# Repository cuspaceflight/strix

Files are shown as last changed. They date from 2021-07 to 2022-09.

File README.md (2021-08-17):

<p align="center">
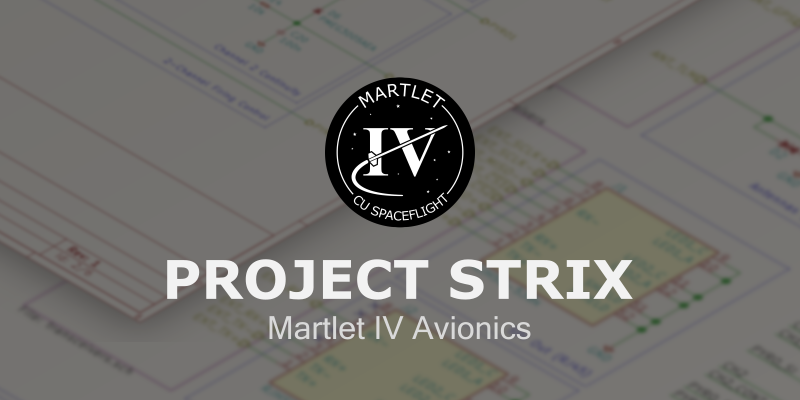
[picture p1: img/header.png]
	
</p>

This repository contains the schematics and firmware for the Martlet IV
Avionics system - Project Strix.

Project Strix is a single-board flight computer designed to carry out essential
tasks during the launch of Martlet IV. Powered by an ARM Cortex-M4, Strix is
able to perform a plethora of functions in real time, and respond to dynamic
events as they happen.

## Specification
The system must be able to
1. Carry out data acquisition for the Pulsar engine sensors.
2. Perform altimetry for the rocket for the purpose of:
	1. Finding the maximum altitude obtained by the rocket.
	2. Deploying the parachutes<sup>*</sup>.
3. Store the data obtained from 1. and 2. using a storage device in a
	protective container.
4. Transmit the data obtained from 1. and 2. to a ground station in
	real-time for the purpose of:
	1. Informing the ground support team of the Pulsar engine sensor
		data before launch (i.e. during filling operations).
	2. To aid an investigation should the rocket vehicle suffer an
		in-flight malfunction.
	3. To find out the rocket's maximum altitude in case loss of
		the rocket prevents retrieval of stored data.

<sup>*</sup>Note that a commercial off-the-shelf 'Stratologger' altimeter
	will also be wired to the parachutes and will also be able to
	deploy them for redundancy.

## Core Modules
The system is composed of several sub-modules, all connected to the central
microcontroller for unified control.

### Altimeter
The onboard altimeter uses two redundant IMUs and barometric pressure sensors
to accurately determine the altitude of the rocket.

### Sensor Front-Ends
The sensor front-ends take data from the Pulsar engine sensors and converts them
into voltages readable by the microcontroller's onboard ADCs. The subsystem
supports the following sensors:

Sensor             | Quantity | Model
------------------ | -------- | --------------------------------------------------------
Pressure Tranducer | 2        | [Omega PXM319-070GI][p_sensor]
Thermocouple       | 4        | [RS Pro K-type welded tip 1/0.315m 5m (762-1118)][t_sensor]

### Radio
The radio subsystem handles the onboard two-way ISM-band radio, which allows
Strix to both send telemetry to ground control and receive telecommands. A
modular architecture allows for precice control of output power to ensure
the rocket operates within local limits. The subsystem also contains a GPS
receiver, which assists in location of the rocket after landing.

### PSU
The modular power supply provides regulated 1.8V, 3.3V, and 12V power to the
flight computer and blackbox. Power is delivered from 2x 18650 Li-ion cells,
which can be recharged on the pad before switching to internal power.

## Design Constraints
The space allowed for the system is shown below (dimensions
in mm):

<p align="center">
	
</p>

The module must also not take up the entire space; some area or a hole
must be left empty to allow other cables to pass through the rocket
(in addition to the central hole).

The module, including any batteries and mounting hardware, should have
as little mass as possible - it must weigh no more than 500g.

[spec]: https://docs.google.com/document/d/1wuNd2ukuNRVKfNca_YTkUf5Qp6ZxcXcQoBAJ7XX6a5Y
[p_sensor]: https://br.omega.com/omegaFiles/pressure/pdf/PXM309.pdf
[t_sensor]: https://docs.rs-online.com/4918/0900766b815bb169.pdf

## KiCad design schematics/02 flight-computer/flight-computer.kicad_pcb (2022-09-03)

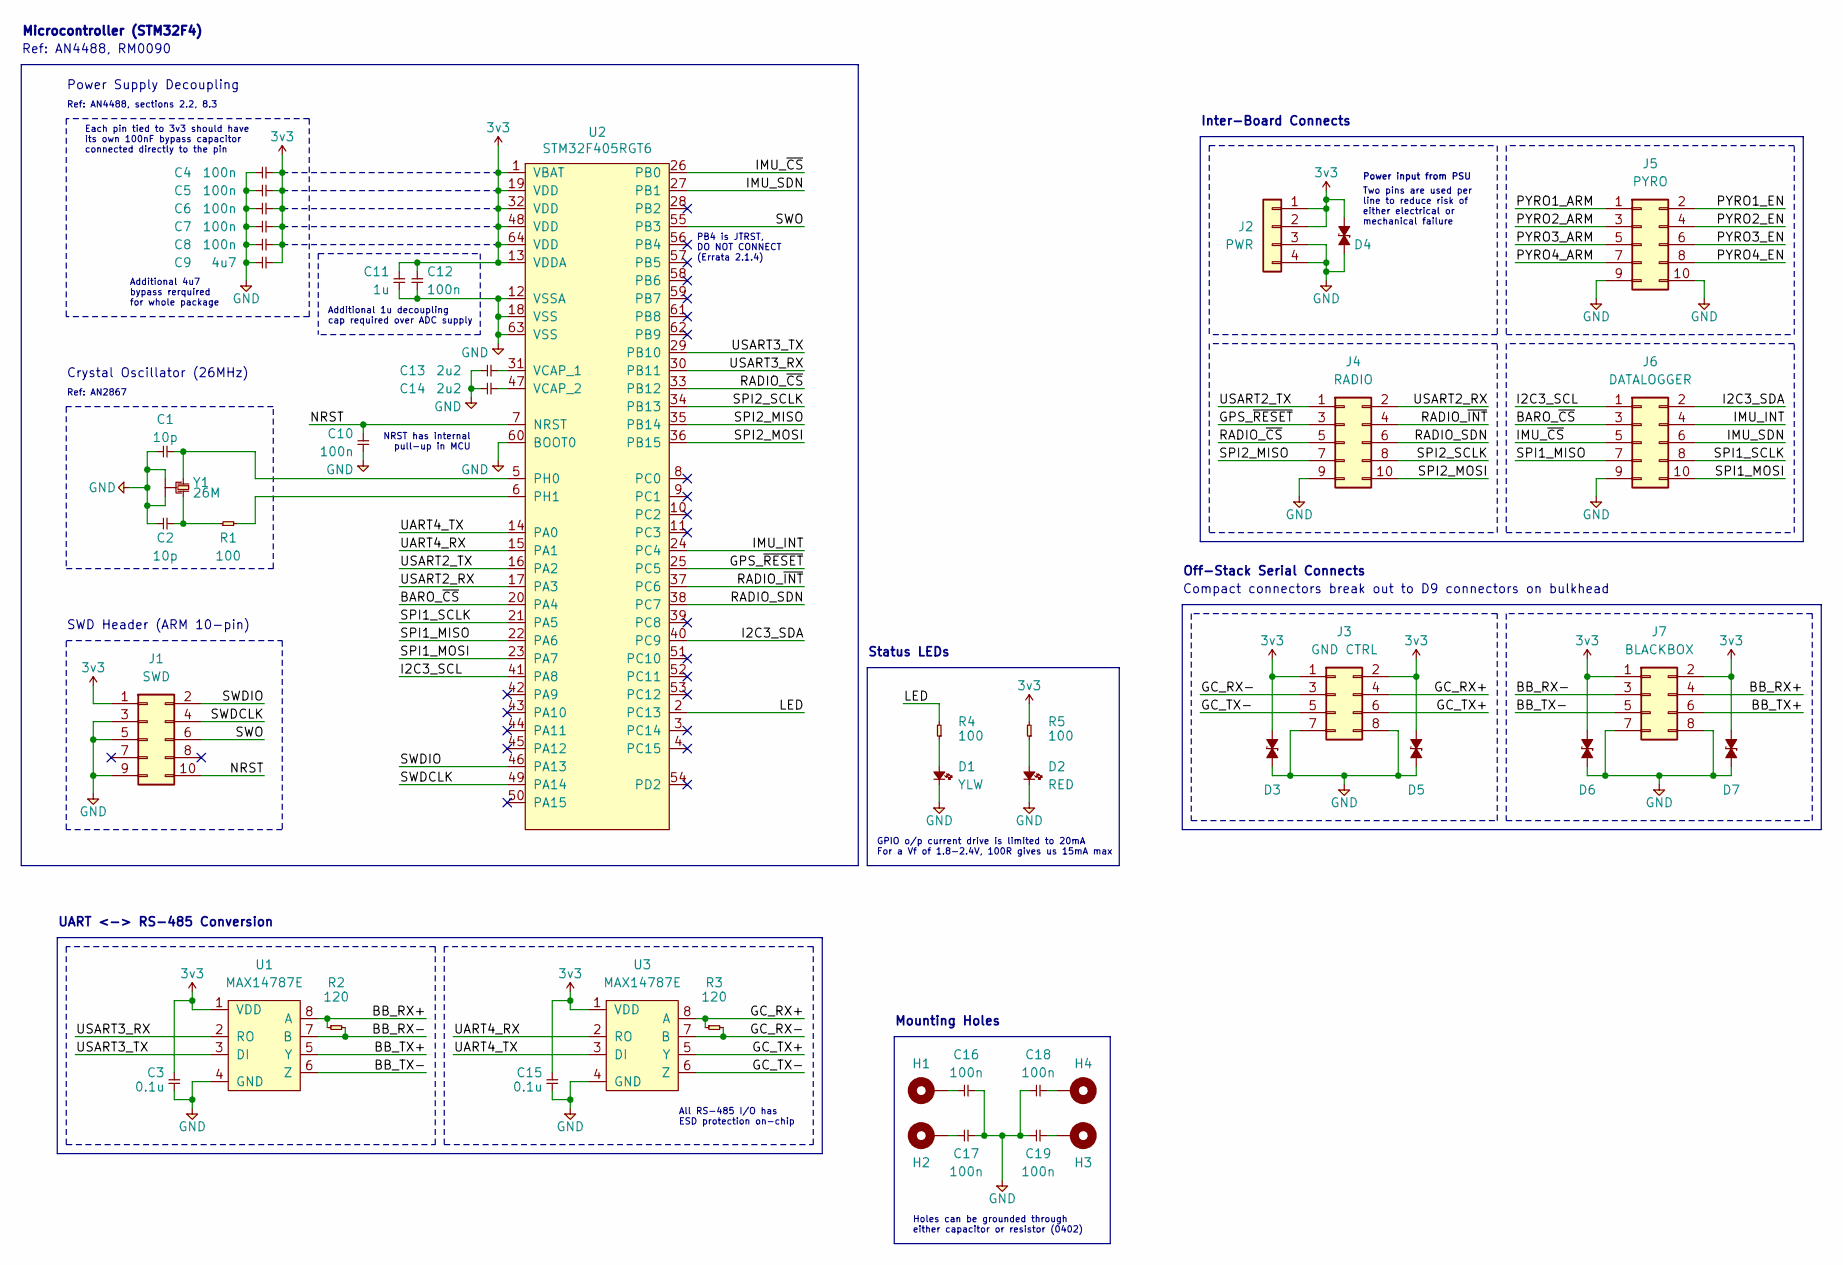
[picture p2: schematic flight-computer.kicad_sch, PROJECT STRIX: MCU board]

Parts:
C1, C2: 10p; C_0402; Farnell 2494183
C3, C15: 0.1u; C_0402; Farnell 2346876
C4, C5, C6, C7, C8, C10, C16, C17, C18, C19: 100n; C_0402; Farnell 2496771
C9: 4u7; C_0402; Farnell 2496771
C11: 1u; C_0402; Farnell 2346876
C12: 100n; C_0402; Farnell 2346876
C13, C14: 2u2; C_0402; Farnell 2362088
D1: YLW; LED_0603; Farnell 3796307
D2: RED; LED_0603; Farnell 3796306
D3, D4, D5, D6, D7: D_ESD; D_0402; Farnell 2368169
H1, H2, H3, H4: MountingHole_Pad
J1: SWD; Header_SWD; Farnell 2856426
J2: PWR; Molex_Nano-Fit_105313-1104
J3: GND CTRL; Molex_Nano-Fit_105314-1108
J4: RADIO; Molex_Nano-Fit_105314-1110
J5: PYRO; Molex_Nano-Fit_105314-1110
J6: DATALOGGER; Molex_Nano-Fit_105314-1110
J7: BLACKBOX; Molex_Nano-Fit_105314-1108
R1: 100; R_0402; Farnell 2447095
R2, R3: 120; R_0402; Farnell 2447103
R4, R5: 100; R_0402; Farnell 2331443
U1, U3: MAX14787E; Farnell 2528531
U2: STM32F405RGT6; Farnell 2064363
Y1: 26M; Xtal_SMD_2016; Farnell 2506952

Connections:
3v3: C3.2, C4.2, C5.2, C6.2, C7.2, C8.2, C9.2, C11.2, C12.2, C15.2, D3.2, D4.2, D5.2, D6.2, D7.2, J1.1, J2.1, J2.2, J3.1, J3.2, J7.1, J7.2, R5.2, U1.1 (VDD), U2.1 (VBAT), U2.13 (VDDA), U2.19 (VDD), U2.32 (VDD), U2.48 (VDD), U2.64 (VDD), U3.1 (VDD)
/BARO_~CS: J6.3, U2.20 (PA4)
/BB_RX+: J7.4, R2.1, U1.8 (A)
/BB_RX-: J7.3, R2.2, U1.7 (B)
/BB_TX+: J7.6, U1.5 (Y)
/BB_TX-: J7.5, U1.6 (Z)
/GC_RX+: J3.4, R3.1, U3.8 (A)
/GC_RX-: J3.3, R3.2, U3.7 (B)
/GC_TX+: J3.6, U3.5 (Y)
/GC_TX-: J3.5, U3.6 (Z)
/GPS_~RESET: J4.3, U2.25 (PC5)
/I2C3_SCL: J6.1, U2.41 (PA8)
/I2C3_SDA: J6.2, U2.40 (PC9)
/IMU_INT: J6.4, U2.24 (PC4)
/IMU_SDN: J6.6, U2.27 (PB1)
/IMU_~CS: J6.5, U2.26 (PB0)
/LED: R4.2, U2.2 (PC13)
/NRST: C10.2, J1.10, U2.7 (NRST)
/PYRO1_ARM: J5.1
/PYRO1_EN: J5.2
/PYRO2_ARM: J5.3
/PYRO2_EN: J5.4
/PYRO3_ARM: J5.5
/PYRO3_EN: J5.6
/PYRO4_ARM: J5.7
/PYRO4_EN: J5.8
/RADIO_SDN: J4.6, U2.38 (PC7)
/RADIO_~CS: J4.5, U2.33 (PB12)
/RADIO_~INT: J4.4, U2.37 (PC6)
/SPI1_MISO: J6.7, U2.22 (PA6)
/SPI1_MOSI: J6.10, U2.23 (PA7)
/SPI1_SCLK: J6.8, U2.21 (PA5)
/SPI2_MISO: J4.7, U2.35 (PB14)
/SPI2_MOSI: J4.10, U2.36 (PB15)
/SPI2_SCLK: J4.8, U2.34 (PB13)
/SWDCLK: J1.4, U2.49 (PA14)
/SWDIO: J1.2, U2.46 (PA13)
/SWO: J1.6, U2.55 (PB3)
/UART4_RX: U2.15 (PA1), U3.2 (RO)
/UART4_TX: U2.14 (PA0), U3.3 (DI)
/USART2_RX: J4.2, U2.17 (PA3)
/USART2_TX: J4.1, U2.16 (PA2)
/USART3_RX: U1.2 (RO), U2.30 (PB11)
/USART3_TX: U1.3 (DI), U2.29 (PB10)
GND: C1.1, C2.1, C3.1, C4.1, C5.1, C6.1, C7.1, C8.1, C9.1, C10.1, C11.1, C12.1, C13.1, C14.1, C15.1, C16.1, C17.1, C18.2, C19.2, D1.1, D2.1, D3.1, D4.1, D5.1, D6.1, D7.1, J1.3, J1.5, J1.9, J2.3, J2.4, J3.7, J3.8, J4.9, J5.9, J5.10, J6.9, J7.7, J7.8, U1.4 (GND), U2.12 (VSSA), U2.18 (VSS), U2.60 (BOOT0), U2.63 (VSS), U3.4 (GND), Y1.2, Y1.4
unnamed: C1.2, U2.5 (PH0), Y1.1
unnamed: C2.2, R1.1, Y1.3
unnamed: C13.2, U2.31 (VCAP_1)
unnamed: C14.2, U2.47 (VCAP_2)
unnamed: C16.2, H1.1
unnamed: C17.2, H2.1
unnamed: C18.1, H4.1
unnamed: C19.1, H3.1
unnamed: D1.2, R4.1
unnamed: D2.2, R5.1
unnamed: R1.2, U2.6 (PH1)

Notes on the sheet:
Ref: AN4488, sections 2.2, 8.3
GPIO o/p current drive is limited to 20mA For a Vf of 1.8-2.4V, 100R gives us 15mA max
Holes can be grounded through either capacitor or resistor (0402)
Ref: AN4488, RM0090
Each pin tied to 3v3 should have its own 100nF bypass capacitor connected directly to the pin
Off-Stack Serial Connects
SWD Header (ARM 10-pin)
Additional 4u7 bypass rerquired for whole package
All RS-485 I/O has ESD protection on-chip
Crystal Oscillator (26MHz)
Microcontroller (STM32F4)
Power Supply Decoupling
Compact connectors break out to D9 connectors on bulkhead
Inter-Board Connects
Status LEDs
Mounting Holes
Two pins are used per line to reduce risk of either electrical or mechanical failure
Power input from PSU
UART <-> RS-485 Conversion
PB4 is JTRST, DO NOT CONNECT (Errata 2.1.4)
Ref: AN2867
Additional 1u decoupling cap required over ADC supply
NRST has internal pull-up in MCU

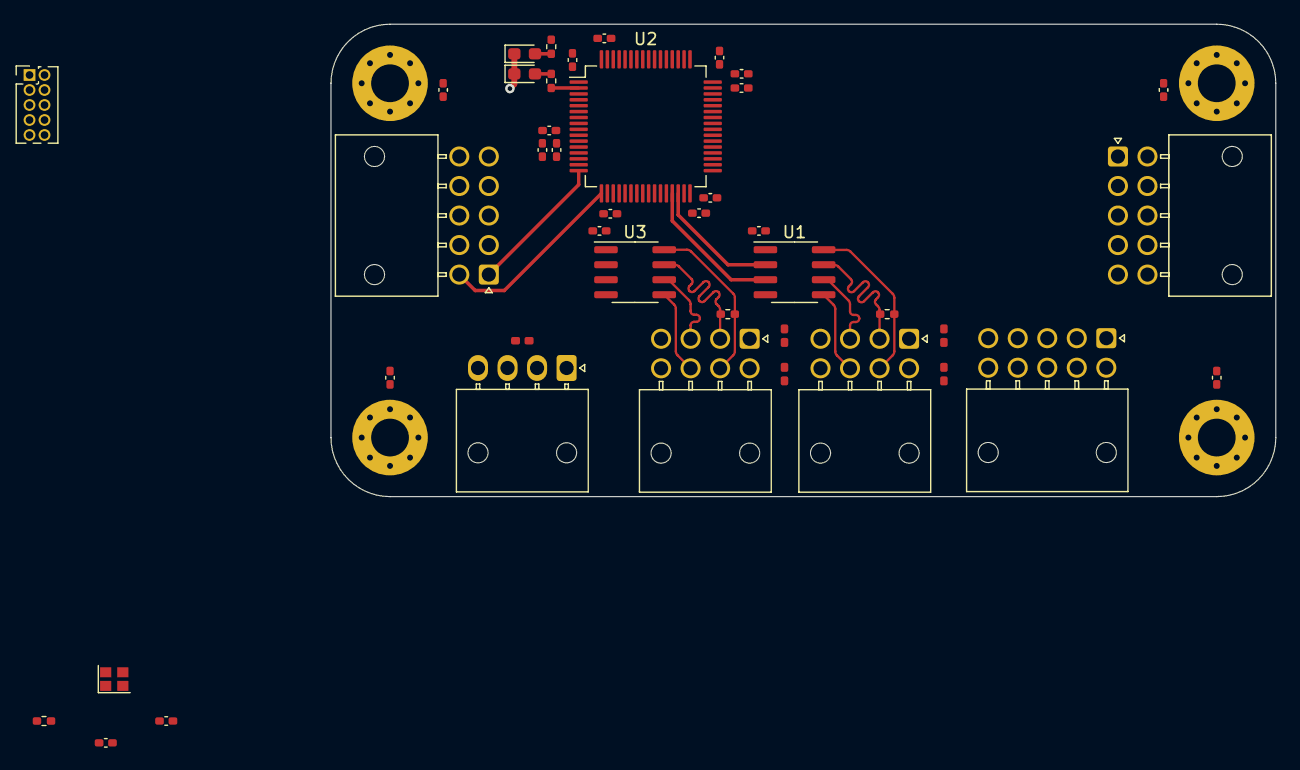
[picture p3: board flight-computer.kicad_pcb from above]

Board: 2 copper layers, 80.0 x 40.0 mm, 46 parts (0 on the bottom side), 48 nets.

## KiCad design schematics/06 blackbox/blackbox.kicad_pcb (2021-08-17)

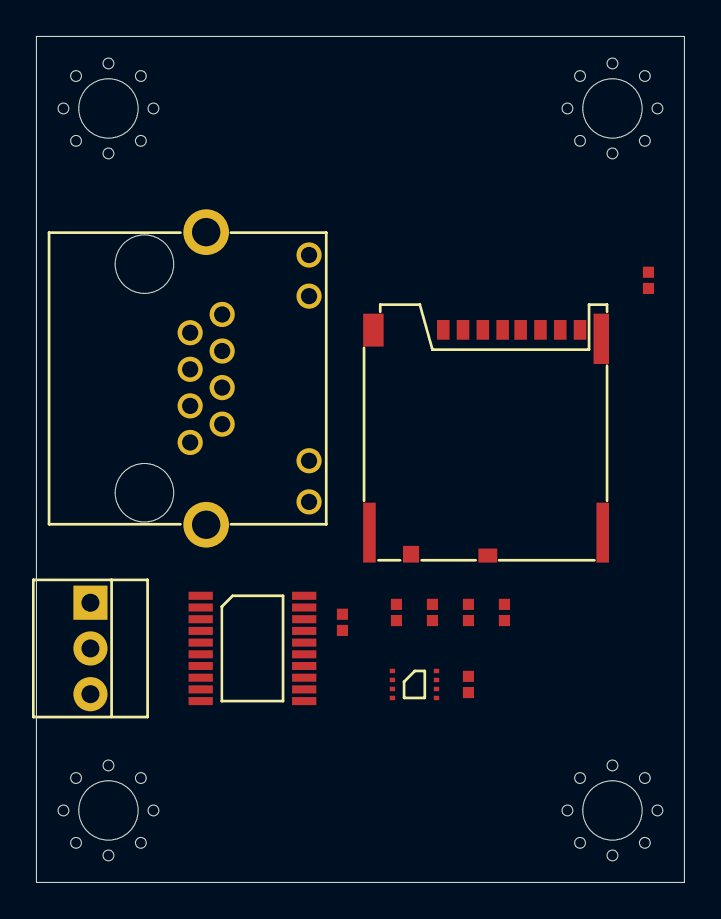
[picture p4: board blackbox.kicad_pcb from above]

Board: 2 copper layers, 36.0 x 47.0 mm, 16 parts (0 on the bottom side), 15 nets, no tracks yet.

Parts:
C1, C2: 100n; 0402
H1, H2, H3, H4: MountingHole_Pad; M3_MOUNT
IC1: SN65LVDT14; TSSOP-20
IC2: W25Q80; UFDFN-8
J1: PWR; MOLEX-KK-254P-03
J2: RJHSE-538x; RJHSE-538X
R1, R2, R3, R4, R5: 47k; 0402
U1: MICROSD; MICROSD_MOLEX_503398-1892

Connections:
3v3: C1.1, C2.1, IC1.13, IC1.17, IC2.8, J1.2, R1.1, R2.1, R3.1, R4.1, R5.1, U1.4
/MISO: IC1.12, IC2.2, R1.2, U1.7
/MISO+: IC1.9, J2.3
/MISO-: IC1.10, J2.6
/MOSI: IC1.18, IC2.5, R5.2, U1.3
/MOSI+: IC1.3, J2.1
/MOSI-: IC1.4, J2.2
/SCLK: IC1.20, IC2.6, U1.5
/SCLK+: IC1.1, J2.8
/SCLK-: IC1.2, J2.7
/~CS1: J2.5, R4.2, U1.2
/~CS2: IC2.1, J2.4
GND: C1.2, C2.2, IC1.11, IC1.15, IC1.19, IC2.4, J1.1, J2.9, J2.10, J2.11, J2.12, J2.S1, J2.S2, U1.6, U1.9
unnamed: R2.2, U1.8
unnamed: R3.2, U1.1

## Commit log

2021-07-21 Restructure schematics; finish FC/Radio
    [dl.sch, ext.sch, fc.sch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]
2021-07-22 Move dl to blackbox; fix minor errors in fc
    [blackbox.kicad_pcb, blackbox.sch, fc.sch]
2021-08-17 Complete redesign
    [altimeter.sch, blackbox.kicad_pcb, blackbox.sch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]
2021-09-17 Add temp rescue symbol while switching libs
    [transceivers.sch]
2021-11-08 Restructure schematics in preparation for new modular system
    [altimeter.sch, blackbox.kicad_pcb, blackbox.sch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]
2021-11-08 Add Strix lib
    [BMI-S-201.STEP, CDCLVC1103PW.STEP, C_0402.STEP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]
2021-11-09 Add preliminary pcb edges
    [altimeter.sch, flight-computer.kicad_pcb, flight-computer.sch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]
2021-11-09 Add I2C pullups to flight computer
    [flight-computer.sch]
2021-12-30 First attempt at layout
    [flight-computer.kicad_pcb, flight-computer.sch]
2022-09-01 Add submodules to match Lychee
    [BMI-S-201.STEP, CDCLVC1103PW.STEP, C_0402.STEP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]
2022-09-01 Create empty KiCad projects for each board
    [altimeter.sch, datalogger.kicad_pcb, datalogger.kicad_sch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]
2022-09-03 Create new flight computer board based on Lychee changes
    [flight-computer.kicad_pcb, flight-computer.kicad_sch, flight-computer.sch]
2022-09-03 Minor schematic revisions
    [flight-computer.kicad_sch]
2022-09-03 Early board layout (without oscillator)
    [flight-computer.kicad_pcb]
2022-09-05 Further schematic work
    [firing_channel.kicad_sch, flight-computer.kicad_sch, radio.kicad_sch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]
2022-09-06 Rough datalogger schematic
    [altimeter.kicad_sch, datalogger.kicad_sch, engine_sensors.kicad_sch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]
